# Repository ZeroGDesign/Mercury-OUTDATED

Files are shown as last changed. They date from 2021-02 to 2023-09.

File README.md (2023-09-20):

# UPDATE AUGUST 2022

The file configurators are live for our EVA 2.4 setup. Please use these from now on: [https://docs.zerog.one/manual/build/mercury_eva/printed_files#-mercury-one1-configurator](https://docs.zerog.one/manual/build/mercury_eva/printed_files#-mercury-one1-configurator)

Or find the cad files here: https://github.com/ZeroGDesign/docs/blob/gh-pages/docs/assets/stl/m1_1/mercury_235_assembly.step

# UPDATE

We're moving towards Mercury 1.1, this will support the Voron Stealthburner and Eva 2.4.

We'd like to recommend you to join our [Discord server](https://discord.io/zerog) for more info on how to build this. We're activly working on our documentation to make our project even better and easier to build for you. Please visit our [Documentation](https://docs.zerog.one/){:target="_blank"} to read more about our current projects.

## Documentation

The new files can be found on our [documentation](https://docs.zerog.one/) under section "manual"  We're activly working on the documentation to make your world easier.



ZeroGDesign/Mercury is licensed under the
GNU General Public License v3.0<br><br>
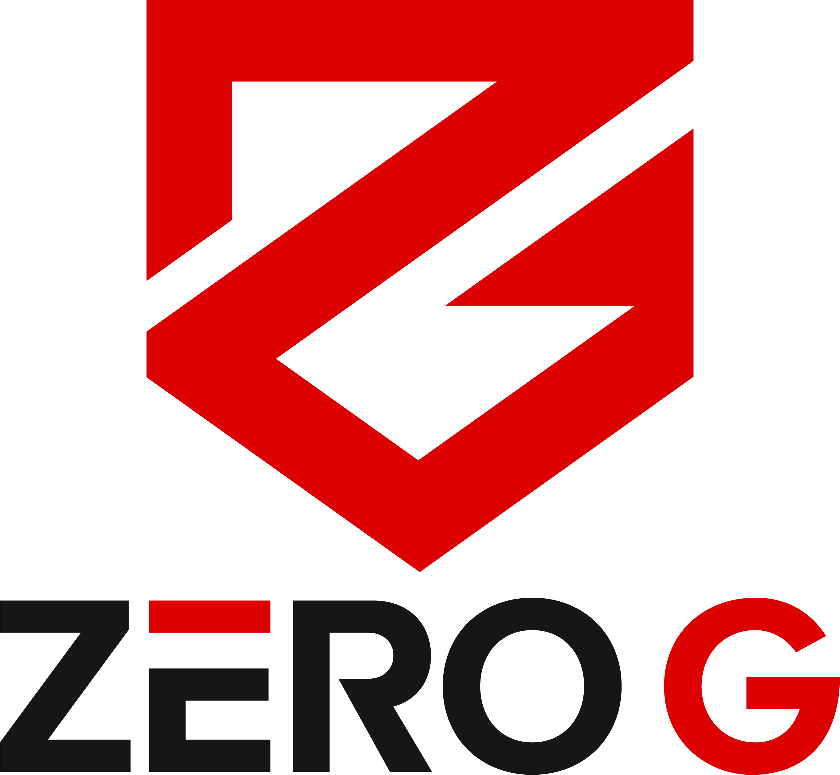
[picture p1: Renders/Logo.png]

____

### Mercury One
<a href="https://discord.io/zerog" target="_blank">Discord Shield</a>
<br>Website: https://zerogdesign.github.io/index.html
____
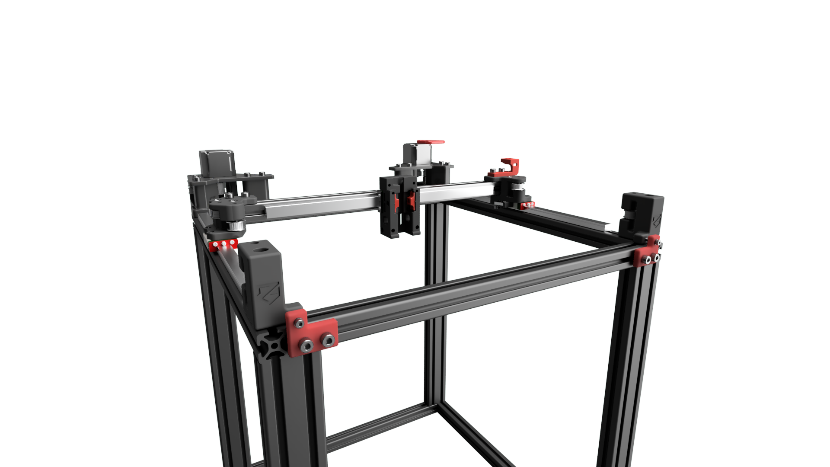
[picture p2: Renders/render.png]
<br><br>
The official release Zero G Mercury One 3D printer inspired by Voron.<br>
This project uses a 370mm x Extrusion and 3 x 300mm MGN12H rails<BR><BR>
Recommended print settings: https://i.imgur.com/dN6sj4v.png

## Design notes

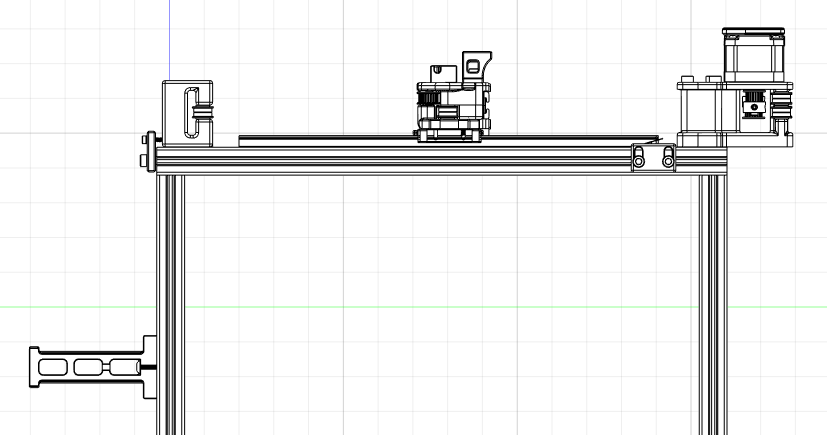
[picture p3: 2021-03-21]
Renders/right_side_view.png

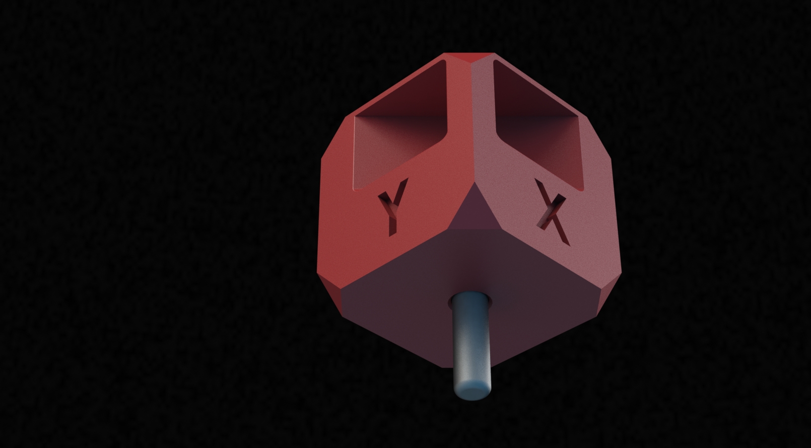
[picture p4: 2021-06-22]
Renders/Cube/ZeroGCube2.JPG

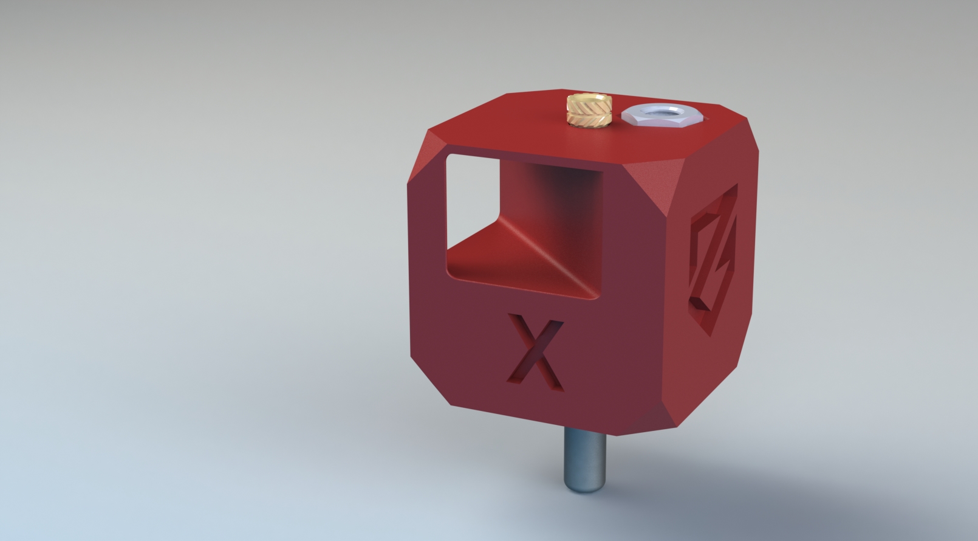
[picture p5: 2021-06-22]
Renders/Cube/ZeroGCube3.JPG

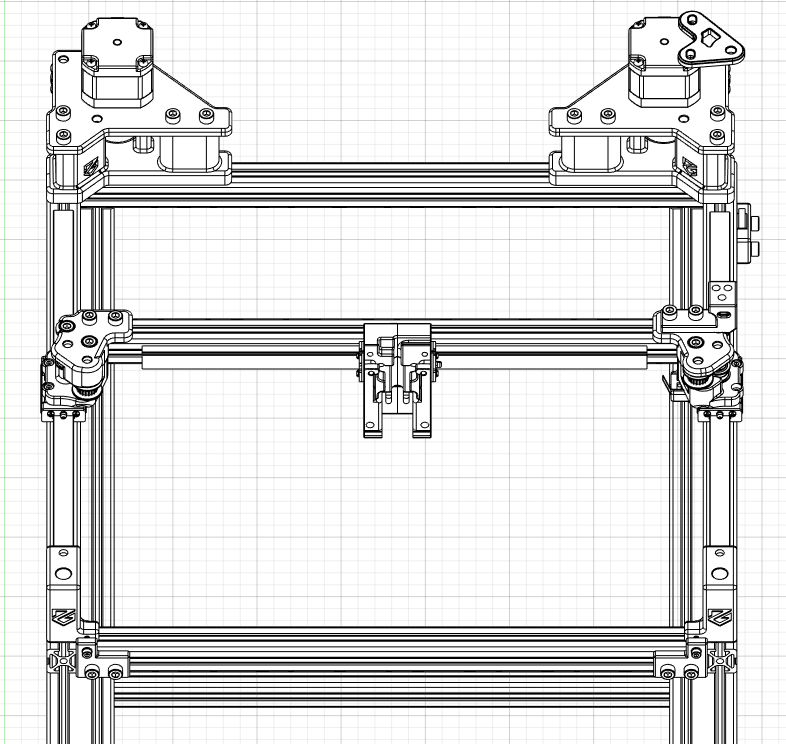
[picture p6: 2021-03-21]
Renders/front_top_view.png

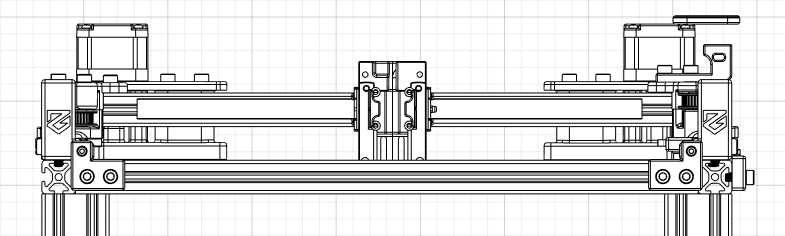
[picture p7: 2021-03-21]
Renders/front_view.png

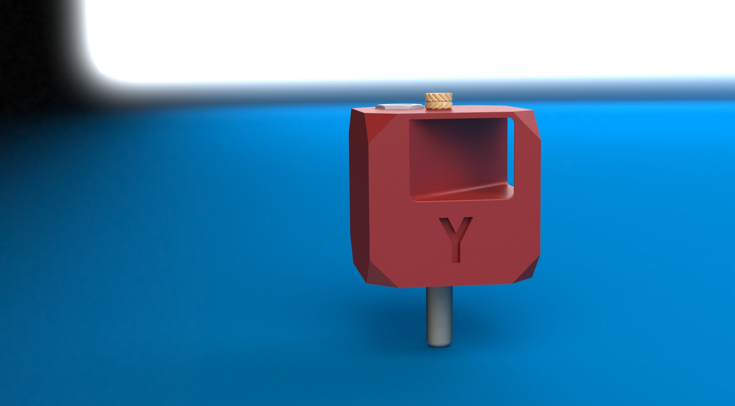
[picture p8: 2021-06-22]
Renders/Cube/ZeroGCube4.JPG

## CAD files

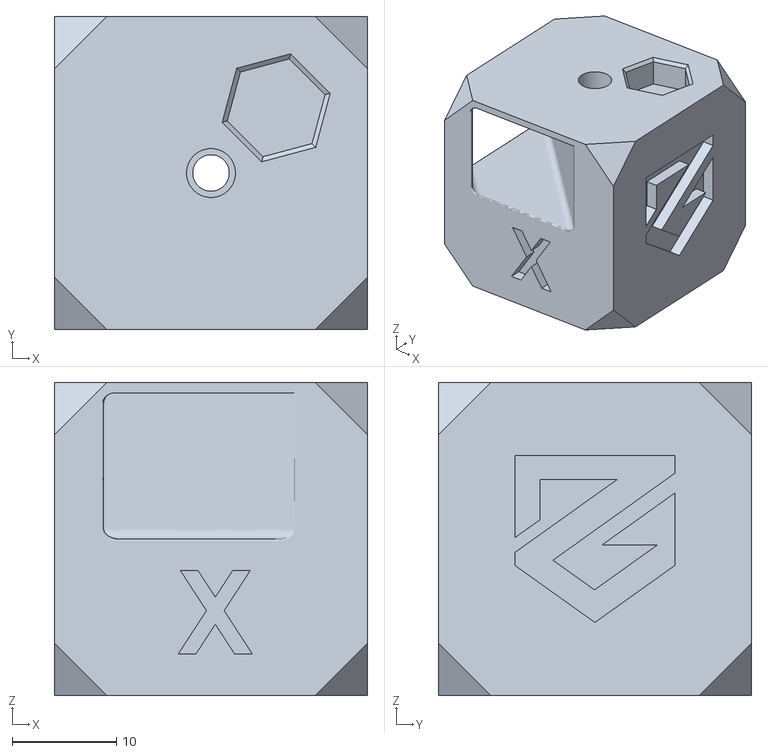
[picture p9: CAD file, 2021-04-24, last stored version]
STLs/CALIBRATION/ZeroGCube30x30.stl
30.0 x 30.0 x 30.0

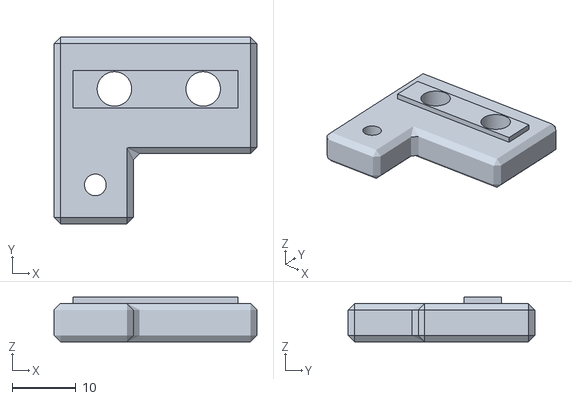
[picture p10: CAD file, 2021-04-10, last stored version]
STLs/MERCURY ONE/Front Idler Towers/Pulley_tension_left.stl
31.8 x 29.3 x 7.00

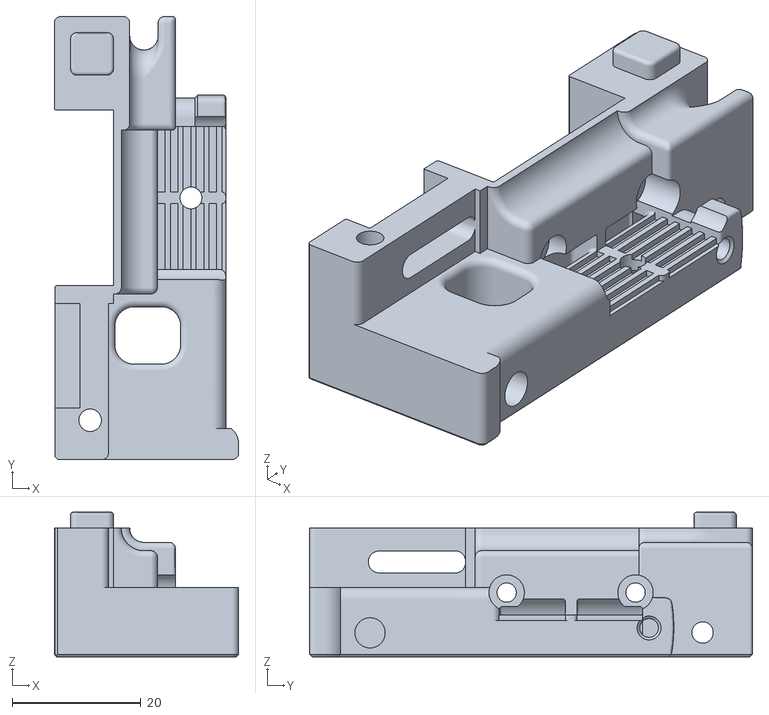
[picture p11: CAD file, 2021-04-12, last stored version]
STLs/MERCURY ONE/Gantry/AFTERBURNER MGN12H MOUNT (CUSTOM)/Right half.stl
28.6 x 68.8 x 22.5

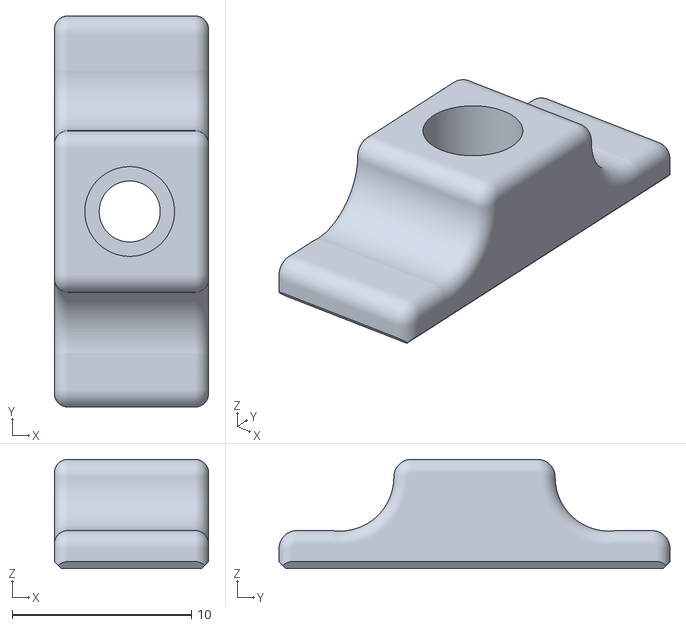
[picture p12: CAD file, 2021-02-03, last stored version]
STLs/MERCURY ONE/Gantry/X_Axis/X_Carriage/belt_clamp_x2.stl
8.60 x 21.8 x 6.10

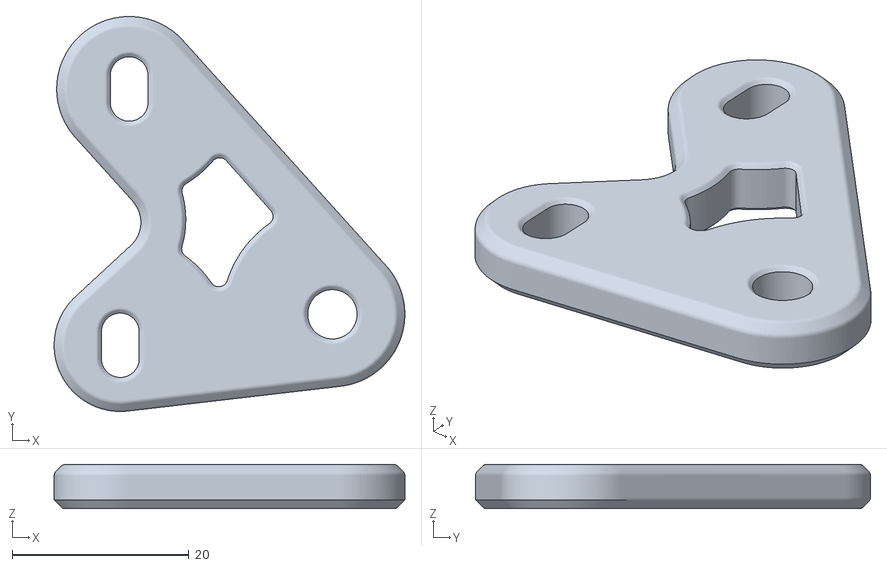
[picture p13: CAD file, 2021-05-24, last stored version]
STLs/MERCURY ONE/Stepper mounts/right_stepper_chain_mount_generic_optional.stl
39.7 x 44.7 x 5.00

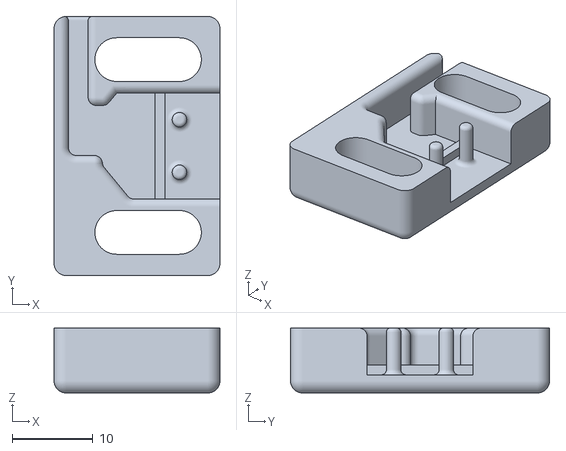
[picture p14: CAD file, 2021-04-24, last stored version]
STLs/MERCURY ONE/Y_Endstop.stl
20.5 x 32.0 x 8.02

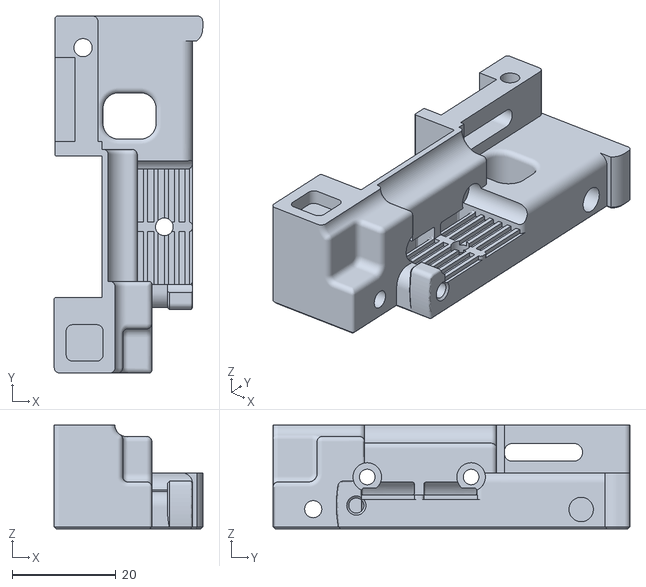
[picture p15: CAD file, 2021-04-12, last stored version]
STLs/MERCURY ONE/Gantry/AFTERBURNER MGN12H MOUNT (CUSTOM)/Left half.stl
28.6 x 68.8 x 20.0

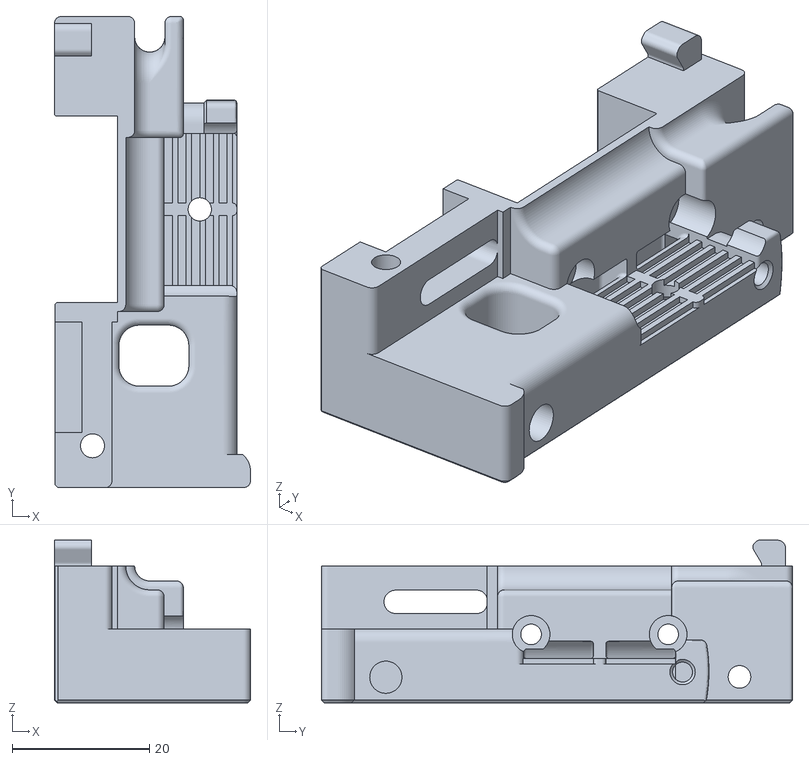
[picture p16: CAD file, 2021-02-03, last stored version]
STLs/MERCURY ONE/Gantry/X_Axis/X_Carriage/x_carriage_frame_right.stl
28.6 x 68.8 x 23.8

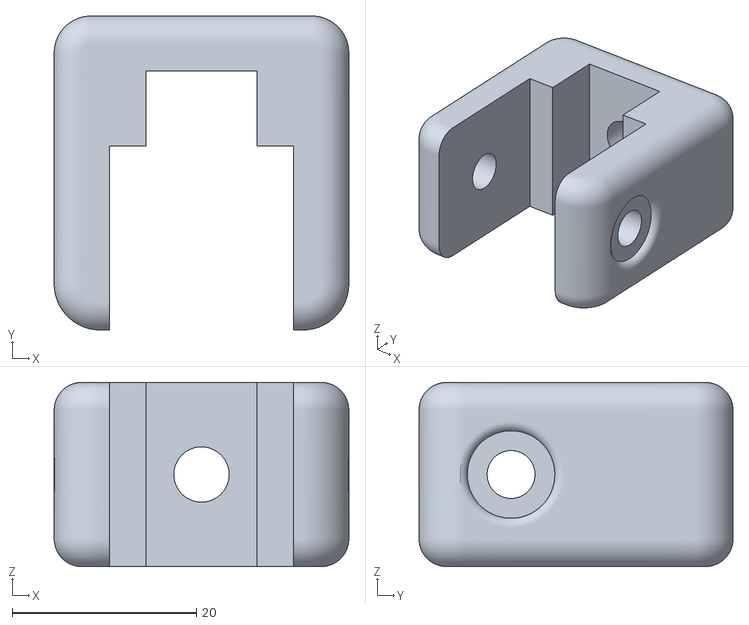
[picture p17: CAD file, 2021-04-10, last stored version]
STLs/MERCURY ONE/Rail alignment tool x 2.stl
32.0 x 34.1 x 20.0

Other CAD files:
STLs/MERCURY ONE/Front Idler Towers/Pulley_tension_right.stl
STLs/MERCURY ONE/Gantry/AFTERBURNER MGN12H MOUNT (CUSTOM)/CLIPX2.stl
STLs/MERCURY ONE/Gantry/X_Axis/X_Carriage/x_carriage_frame_left.stl
STLs/MERCURY1/Gantry/X_Axis/X_Carriage/test.stl
STLs/MERCURY1/Gantry/X_Axis/X_Carriage/x_carriage_frame_left.stl

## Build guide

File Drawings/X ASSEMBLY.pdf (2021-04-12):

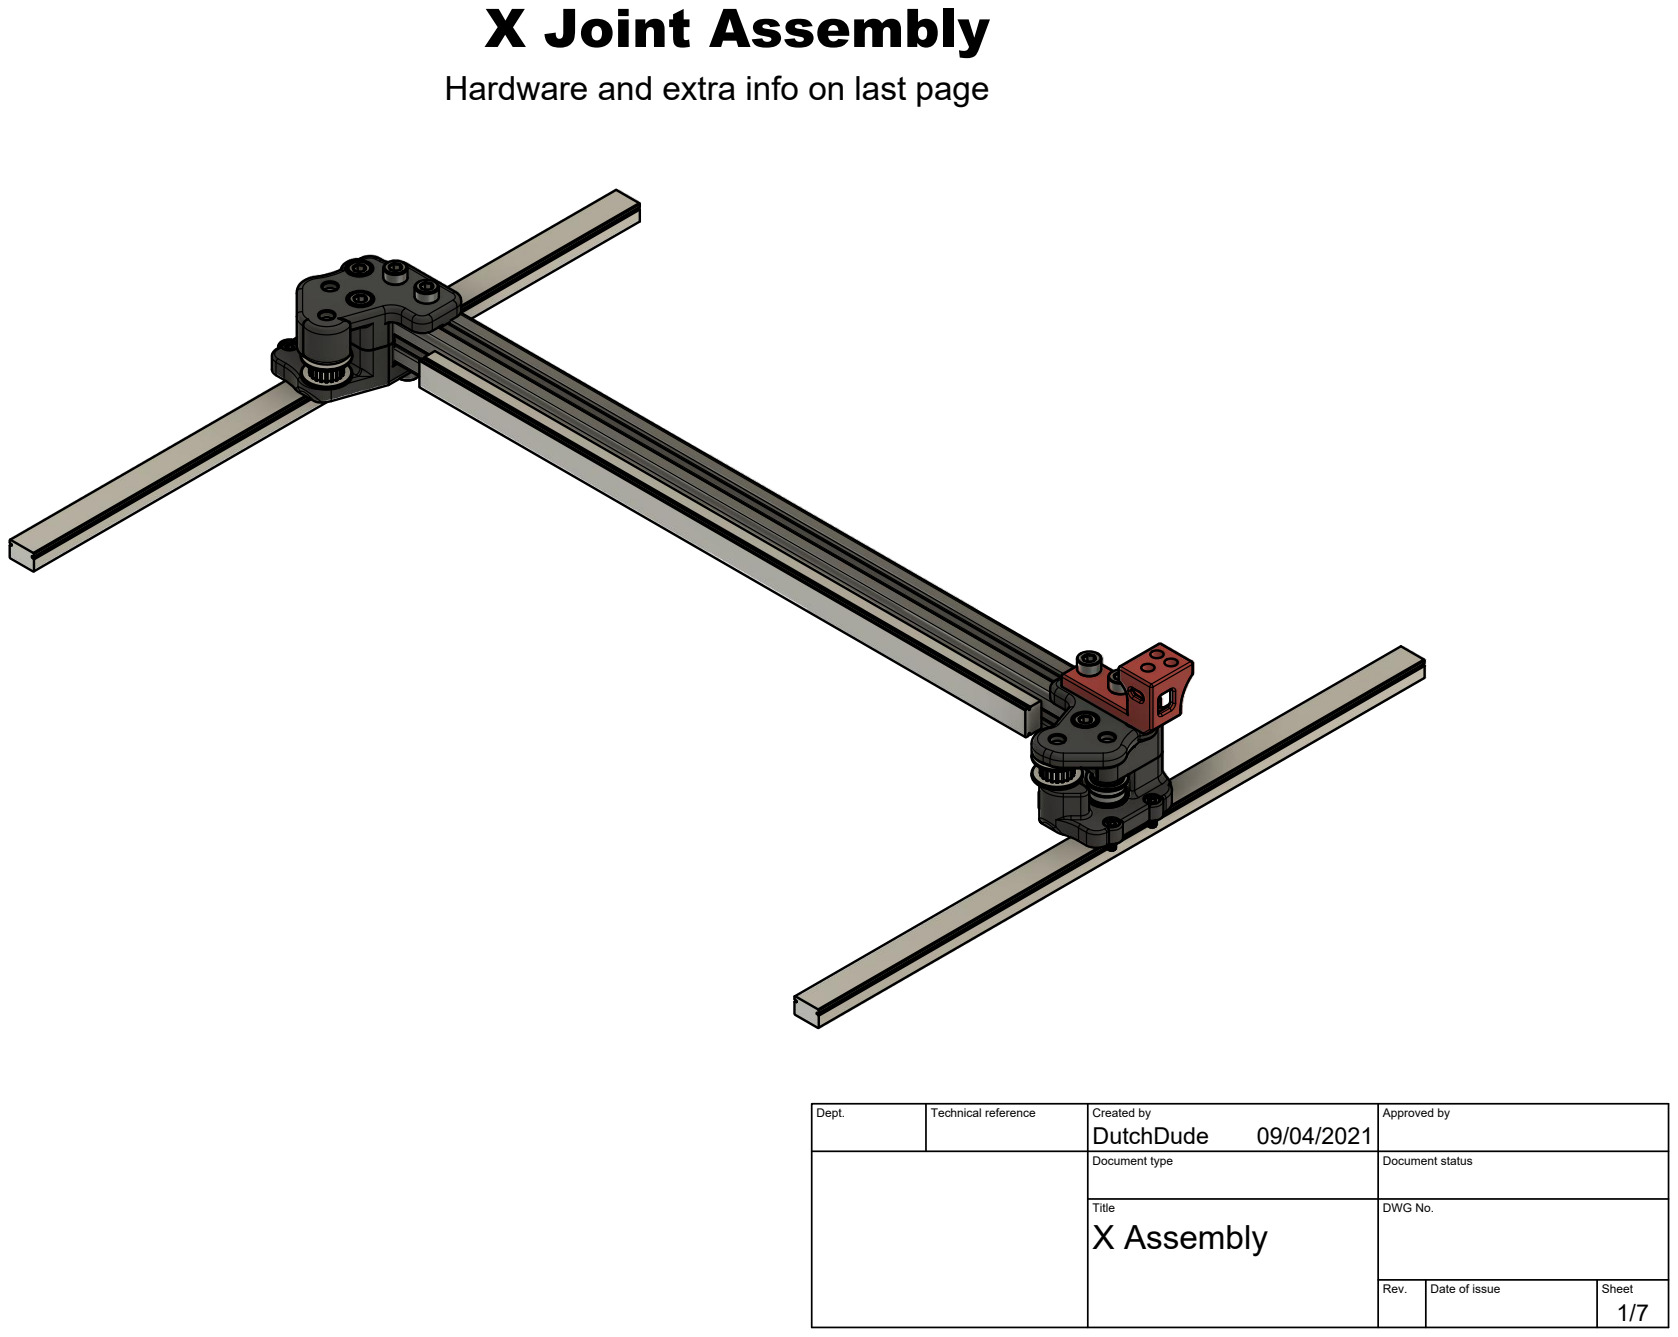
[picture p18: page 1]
X Joint Assembly

Hardware and extra info on last page

Dept. | Technical reference | Created by DutchDude 09/04/2021 | Approved by

Document type | Document status

Title X Assembly | DWG No.

Rev. | Date of issue | Sheet

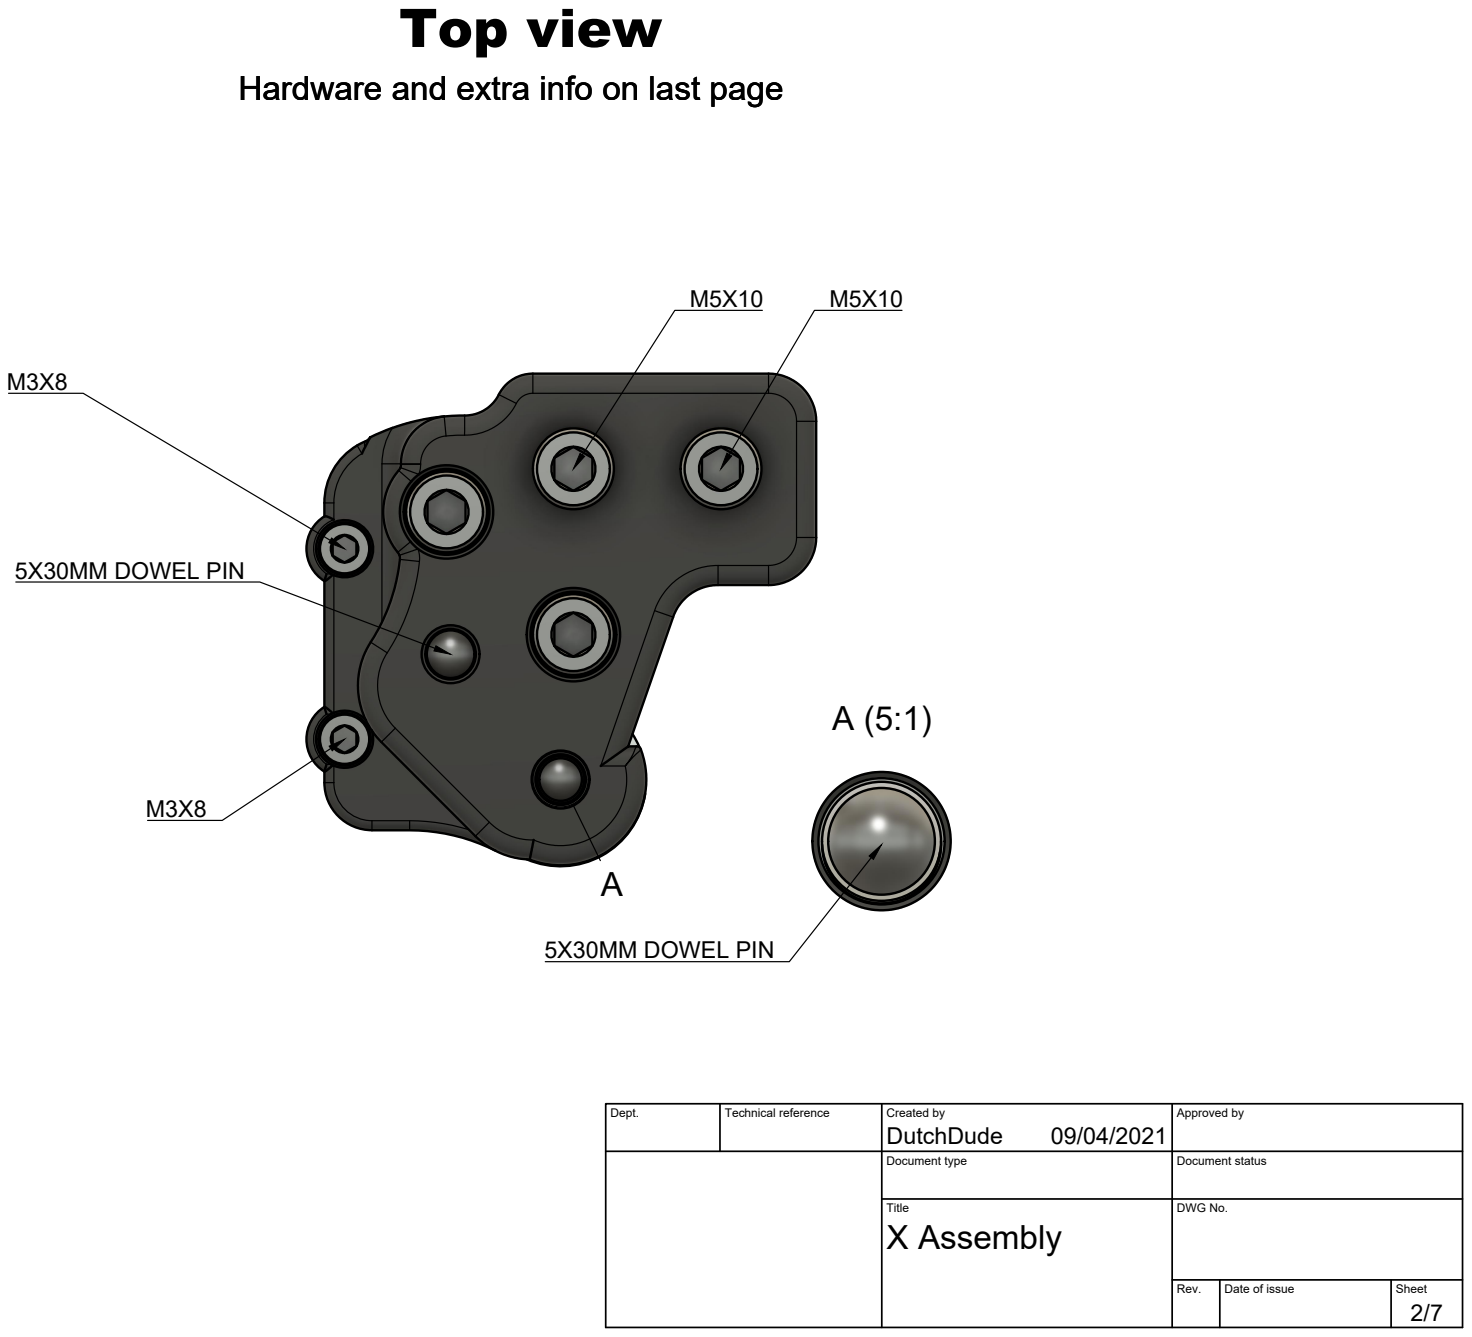
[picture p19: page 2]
Top view; 5X30MM DOWEL PIN

Hardware and extra info on last page

Dept. | Technical reference | Created by DutchDude 09/04/2021 | Approved by

Document type | Document status

Title X Assembly | DWG No.

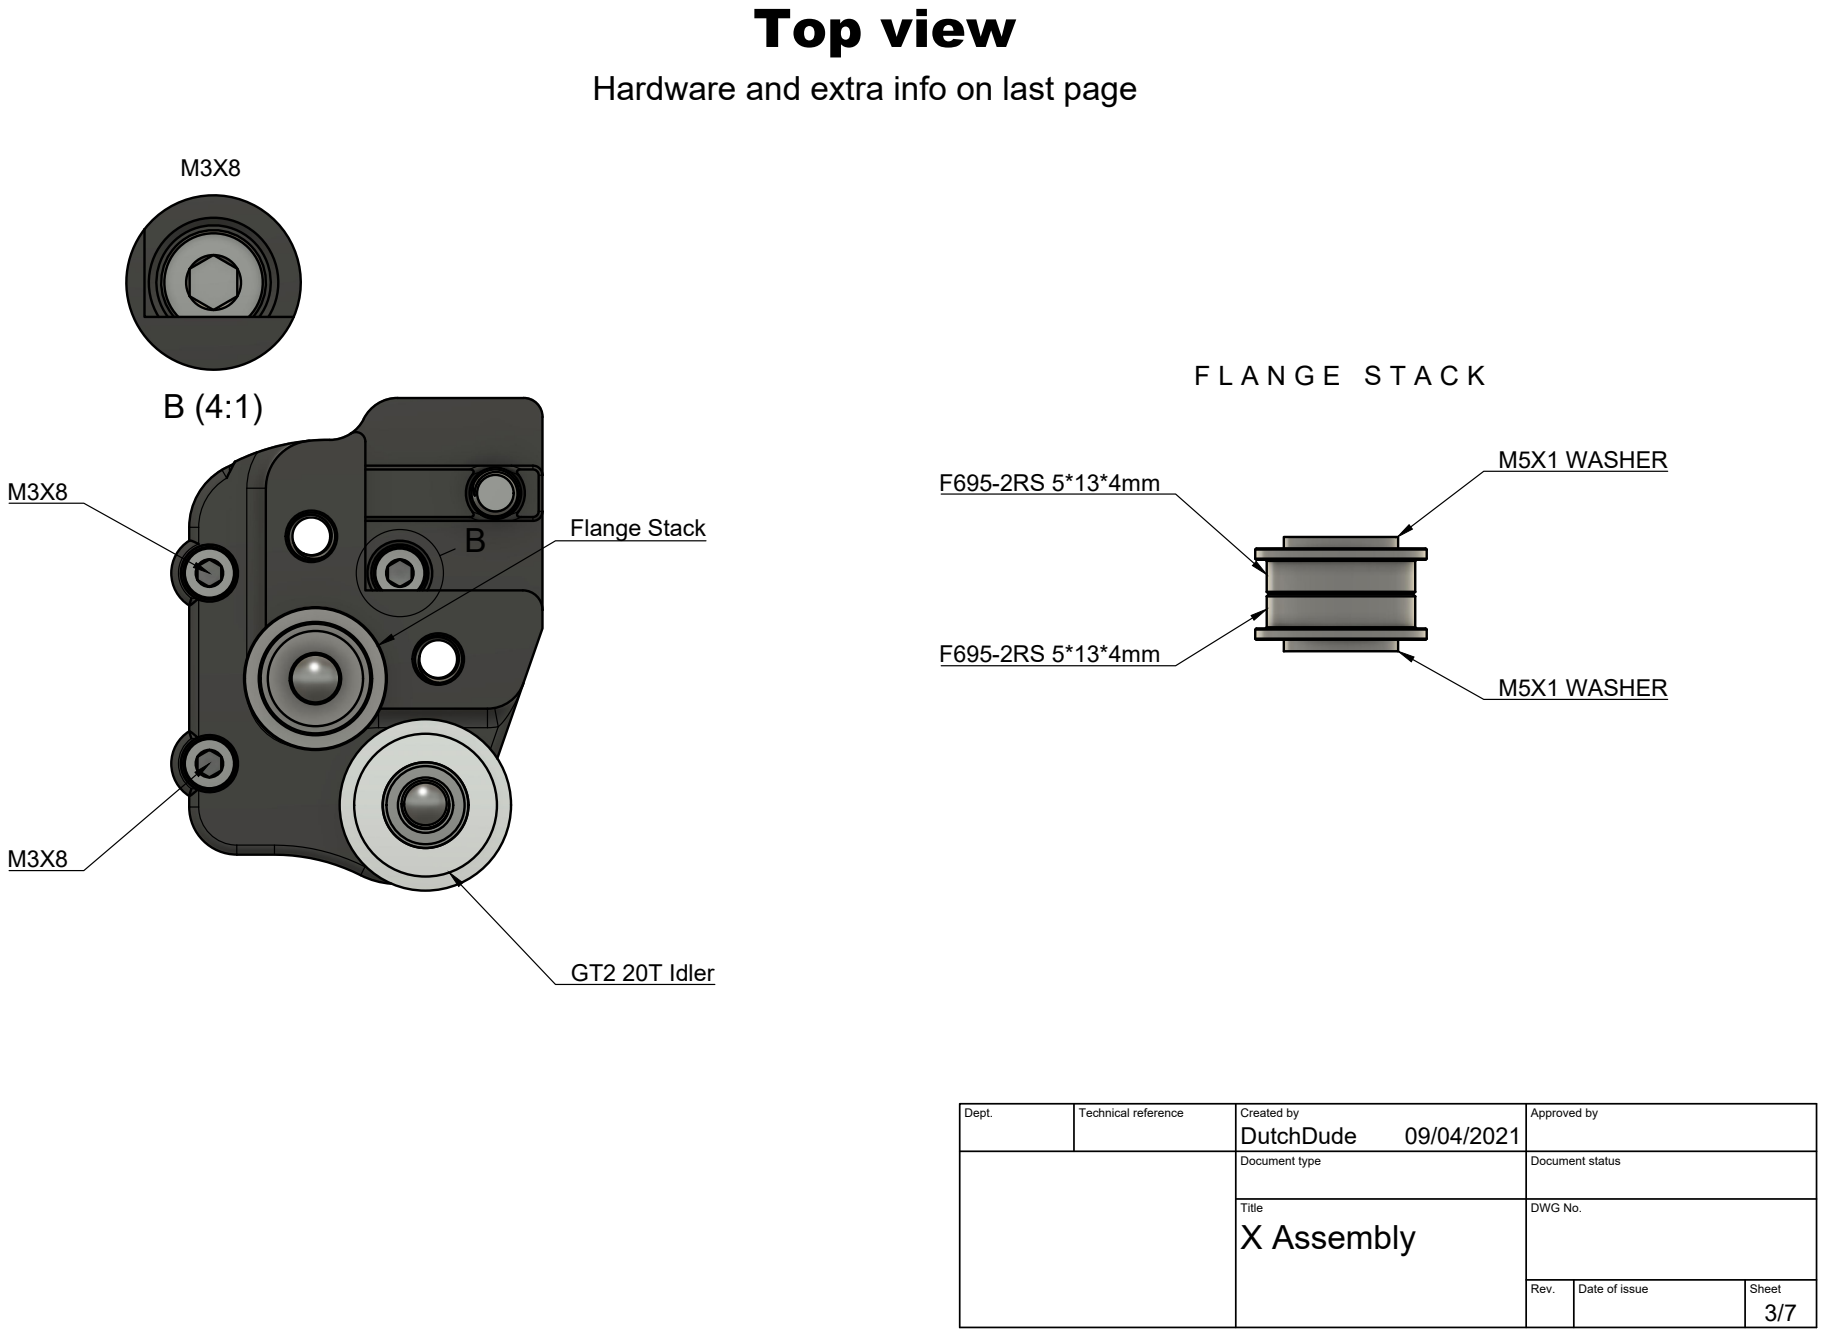
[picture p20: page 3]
Top view; Flange Stack; GT2 20T Idler; M5X1 WASHER

Hardware and extra info on last page

Dept. | Technical reference | Created by DutchDude 09/04/2021 | Approved by

Document type | Document status

Title X Assembly | DWG No.

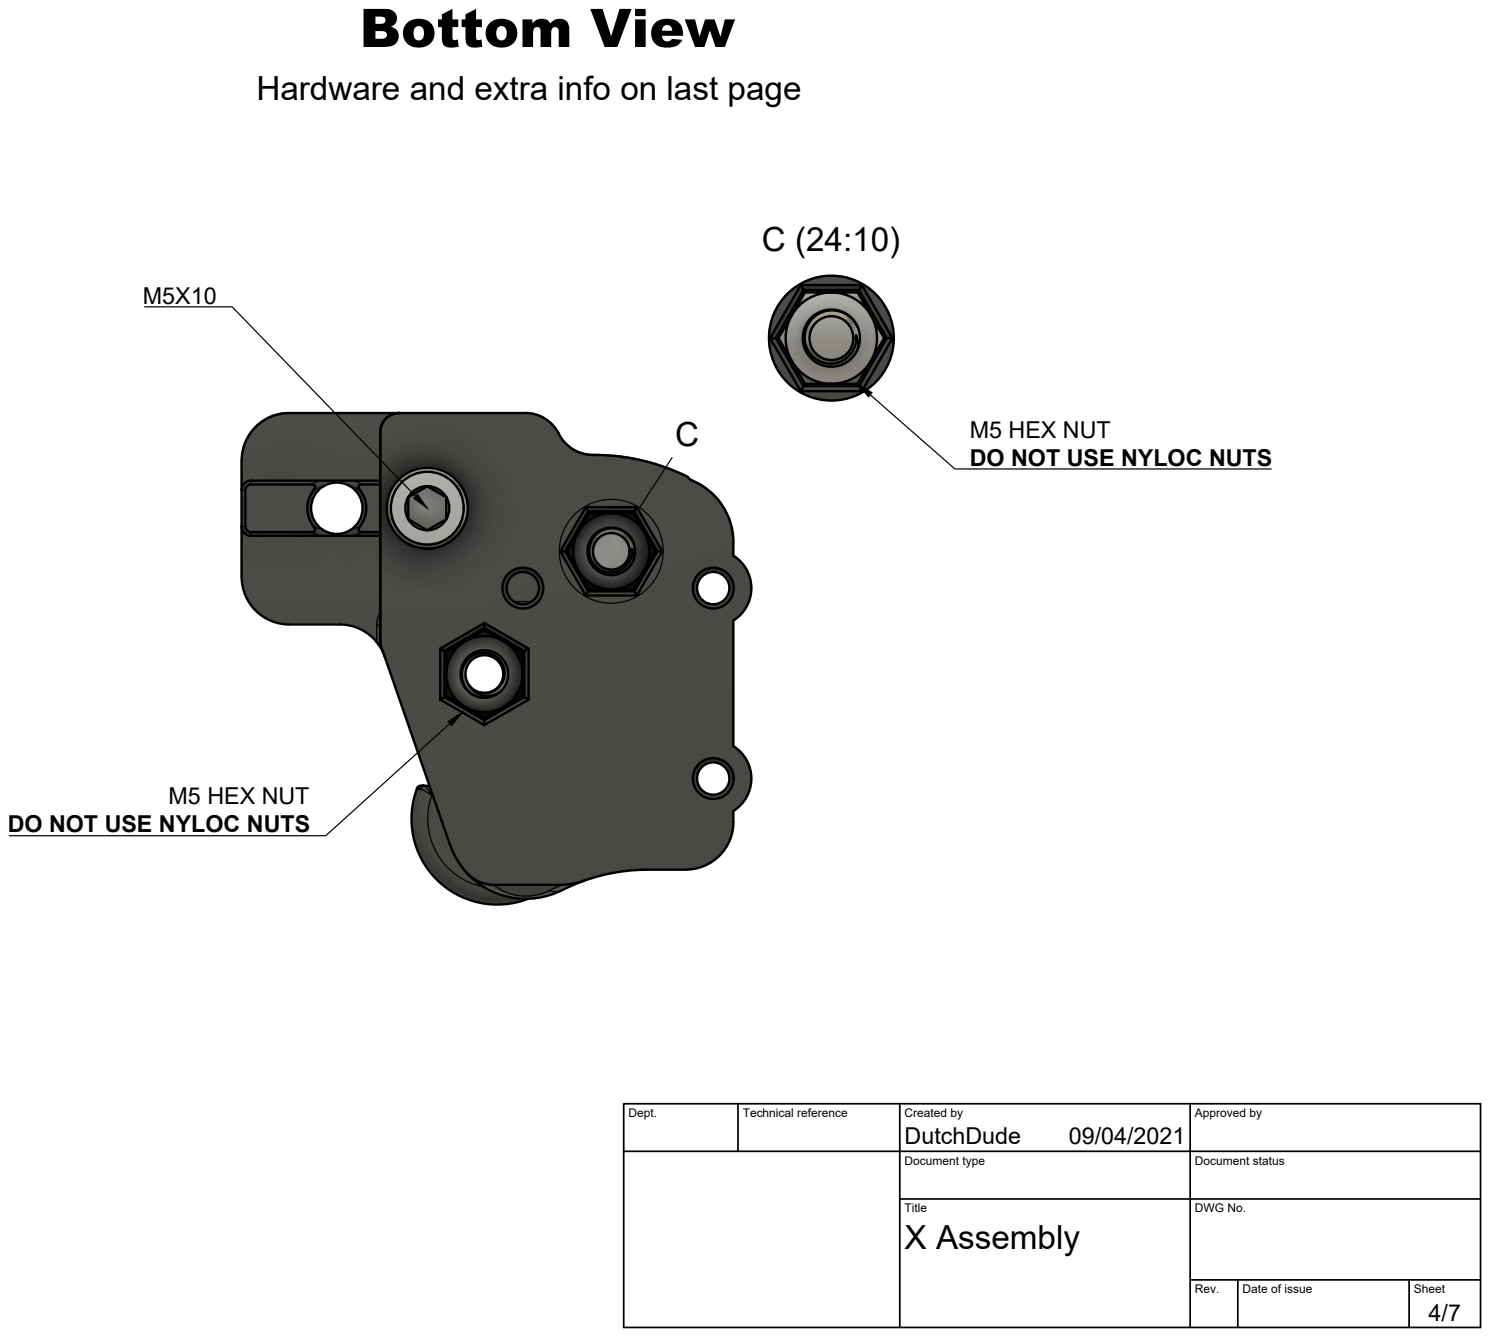
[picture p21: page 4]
Bottom View; M5 HEX NUT

Hardware and extra info on last page

M5 HEX NUT
DO NOT USE NYLOC NUTS

Dept. | Technical reference | Created by DutchDude 09/04/2021 | Approved by

Document type | Document status

Title X Assembly | DWG No.

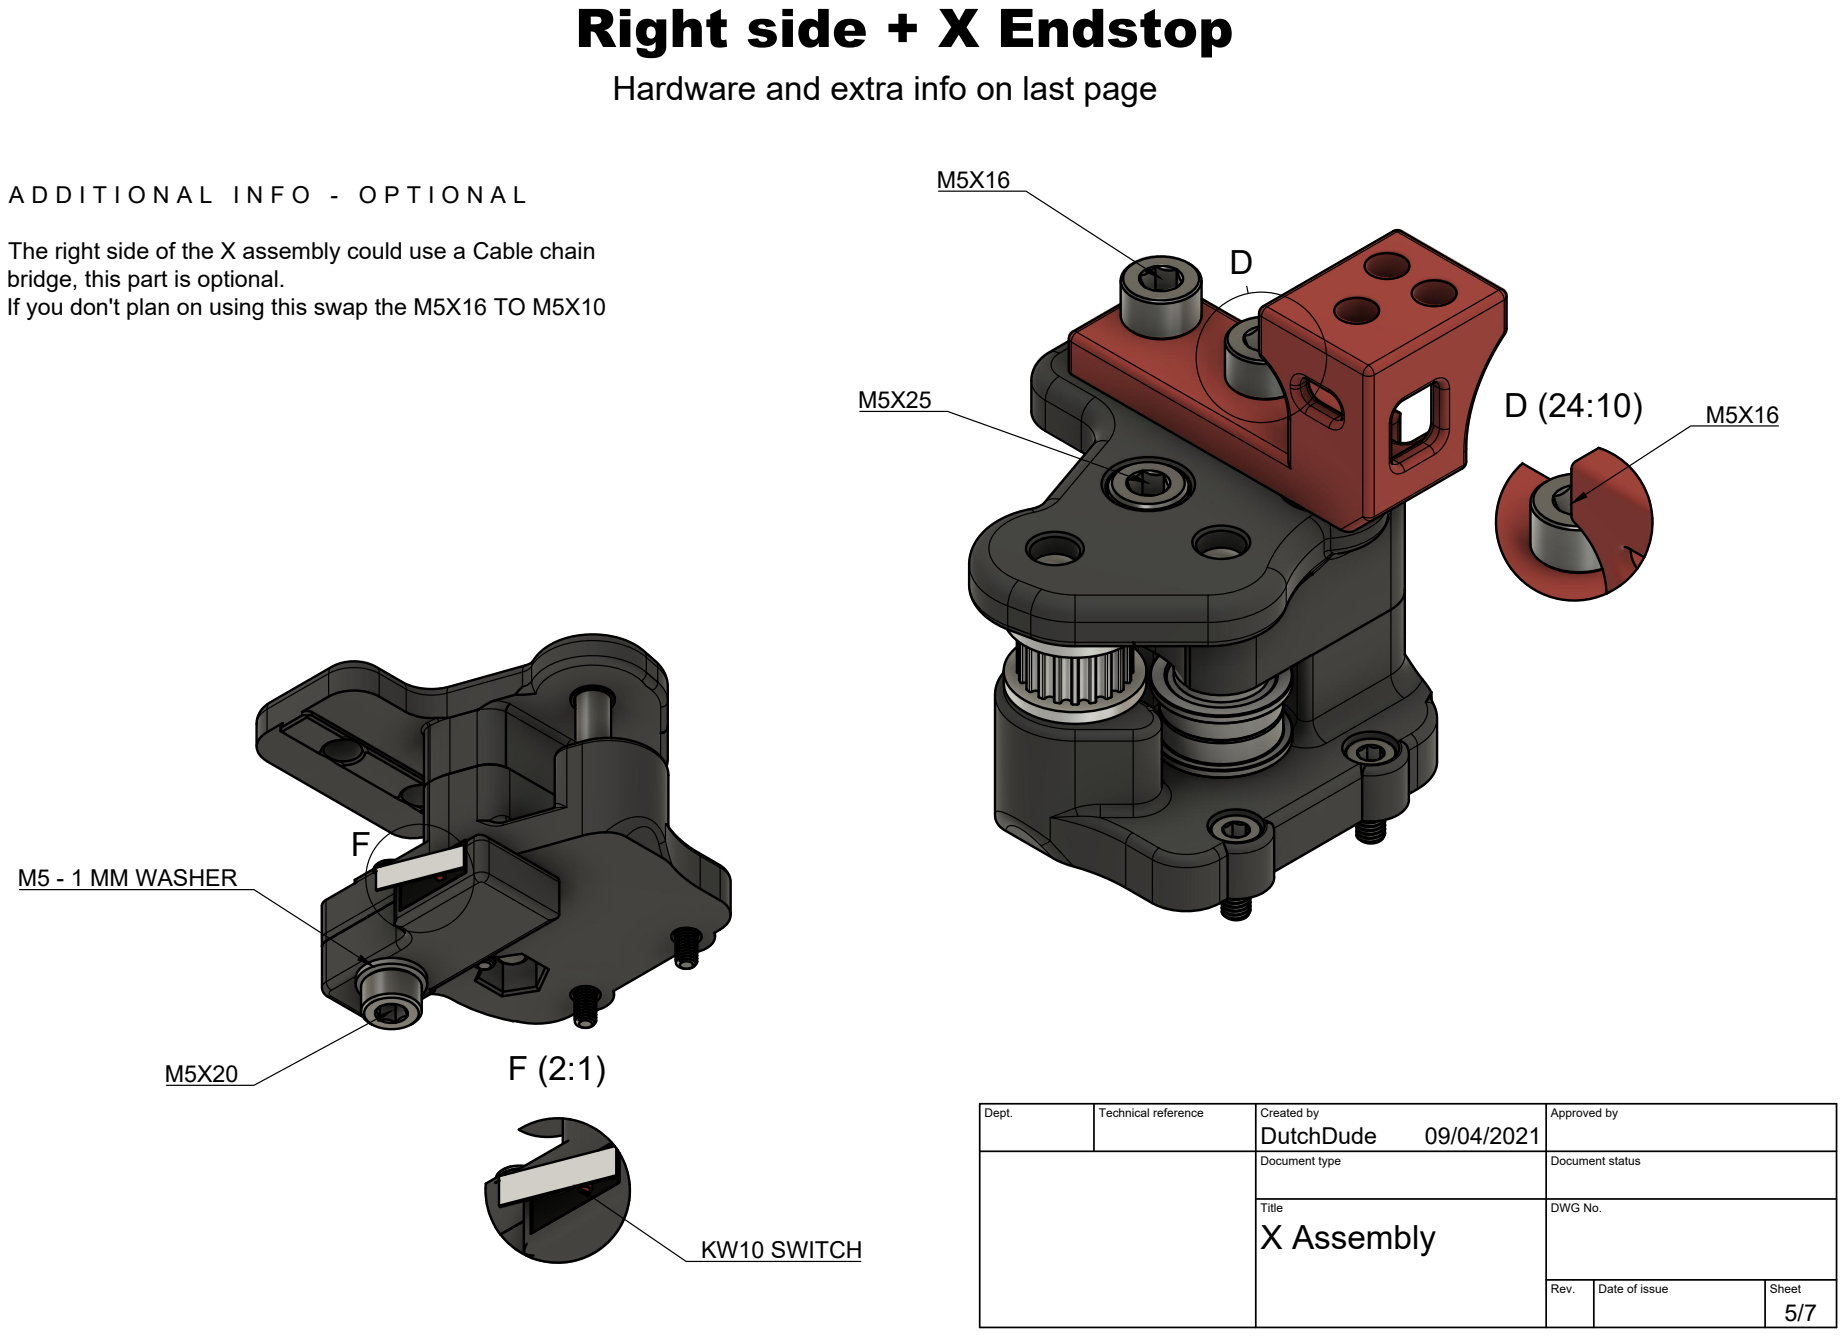
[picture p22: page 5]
KW10 SWITCH; M5 - 1 MM WASHER

Right side + X Endstop

Hardware and extra info on last page

The right side of the X assembly could use a Cable chain
bridge, this part is optional.
If you don't plan on using this swap the M5X16 TO M5X10

Dept. | Technical reference | Created by DutchDude 09/04/2021 | Approved by

Document type | Document status

Title X Assembly | DWG No.

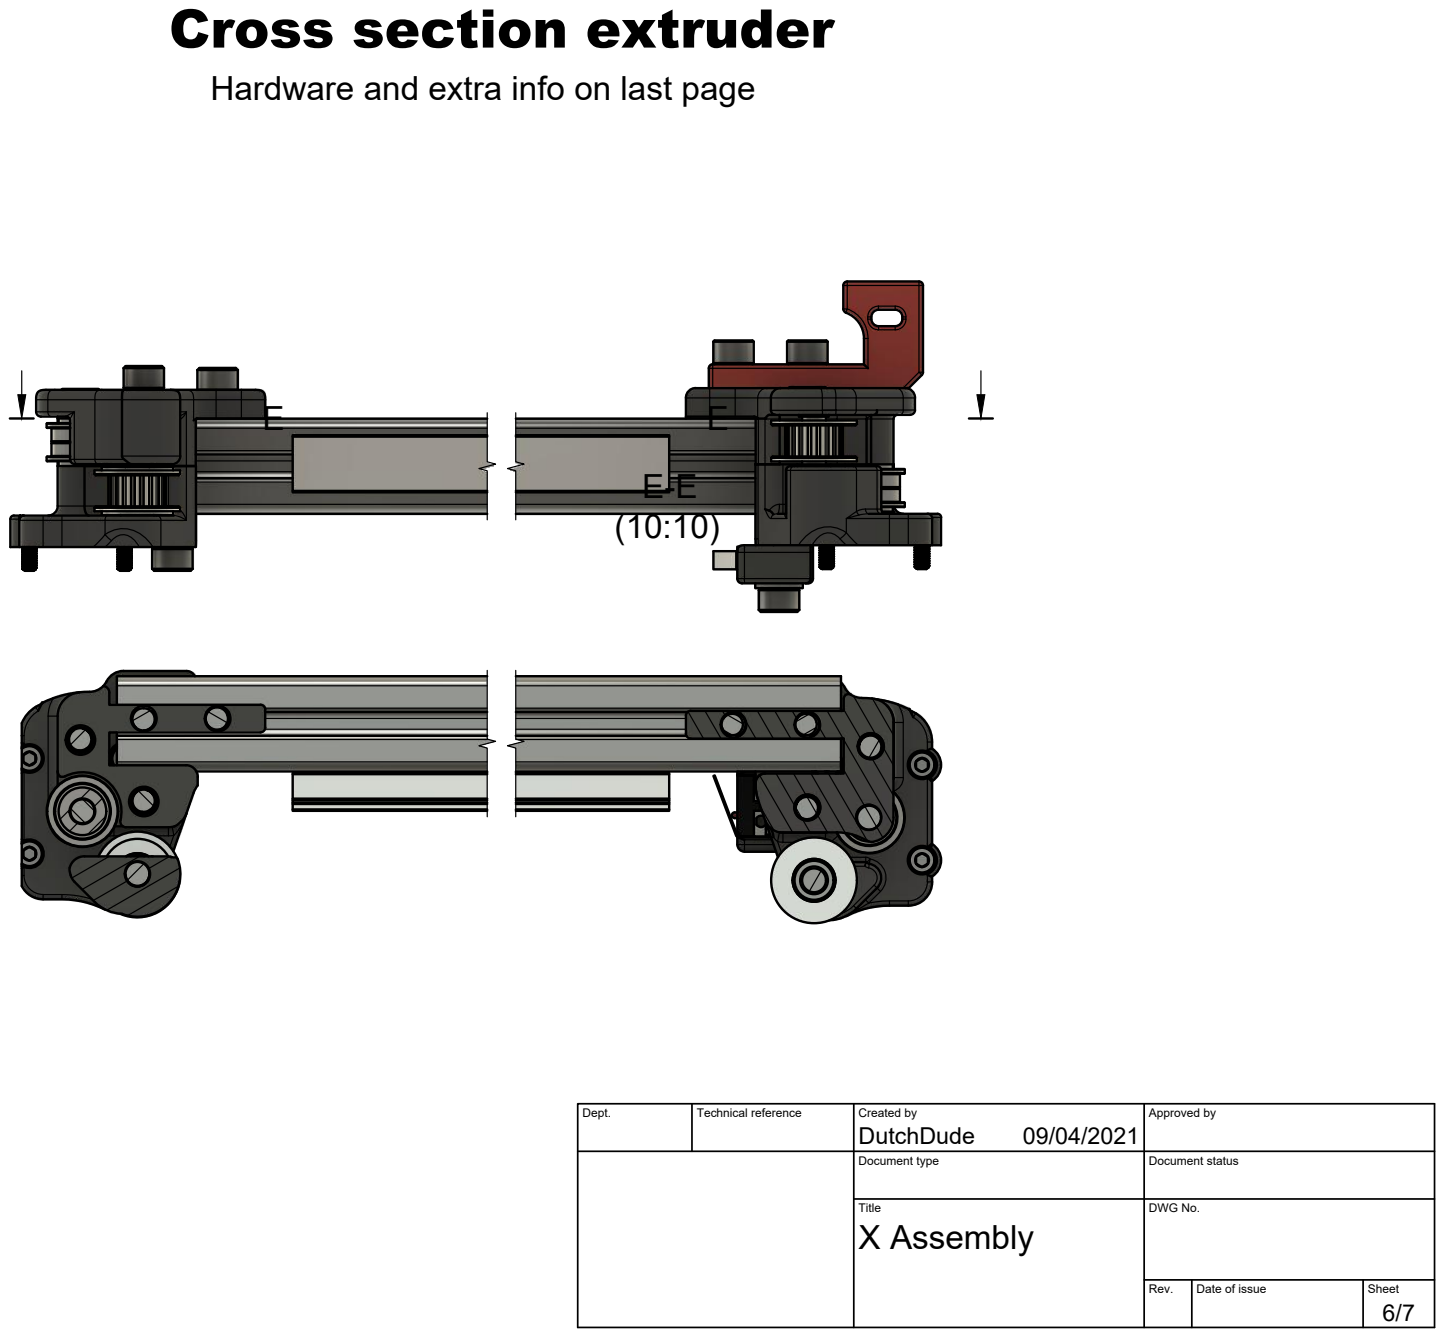
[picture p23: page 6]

Cross section extruder

Hardware and extra info on last page

Dept. | Technical reference | Created by DutchDude 09/04/2021 | Approved by

Document type | Document status

Title X Assembly | DWG No.

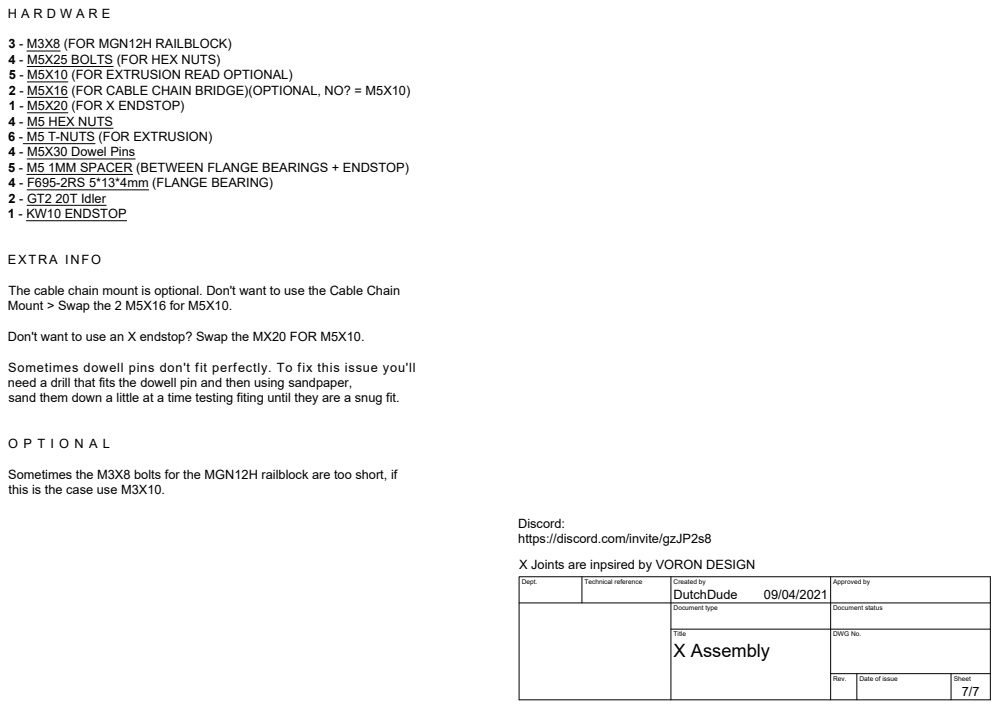
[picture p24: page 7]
EXTRA INFO

3 - M3X8 (FOR MGN12H RAILBLOCK)
4 - M5X25 BOLTS (FOR HEX NUTS)
5 - M5X10 (FOR EXTRUSION READ OPTIONAL)
2 - M5X16 (FOR CABLE CHAIN BRIDGE)(OPTIONAL, NO? = M5X10)
1 - M5X20 (FOR X ENDSTOP)
4 - M5 HEX NUTS
6 - M5 T-NUTS (FOR EXTRUSION)
4 - M5X30 Dowel Pins
5 - M5 1MM SPACER (BETWEEN FLANGE BEARINGS + ENDSTOP)
4 - F695-2RS 5*13*4mm (FLANGE BEARING)
2 - GT2 20T Idler
1 - KW10 ENDSTOP

The cable chain mount is optional. Don't want to use the Cable Chain
Mount > Swap the 2 M5X16 for M5X10.

Don't want to use an X endstop? Swap the MX20 FOR M5X10.

Sometimes dowell pins don't fit perfectly. To fix this issue you'll
need a drill that fits the dowell pin and then using sandpaper,
sand them down a little at a time testing fiting until they are a snug fit.

Sometimes the M3X8 bolts for the MGN12H railblock are too short, if
this is the case use M3X10.

Discord:
https://discord.com/invite/gzJP2s8

X Joints are inpsired by VORON DESIGN

Dept. | Technical reference | Created by DutchDude 09/04/2021 | Approved by

Document type | Document status

Title X Assembly | DWG No.

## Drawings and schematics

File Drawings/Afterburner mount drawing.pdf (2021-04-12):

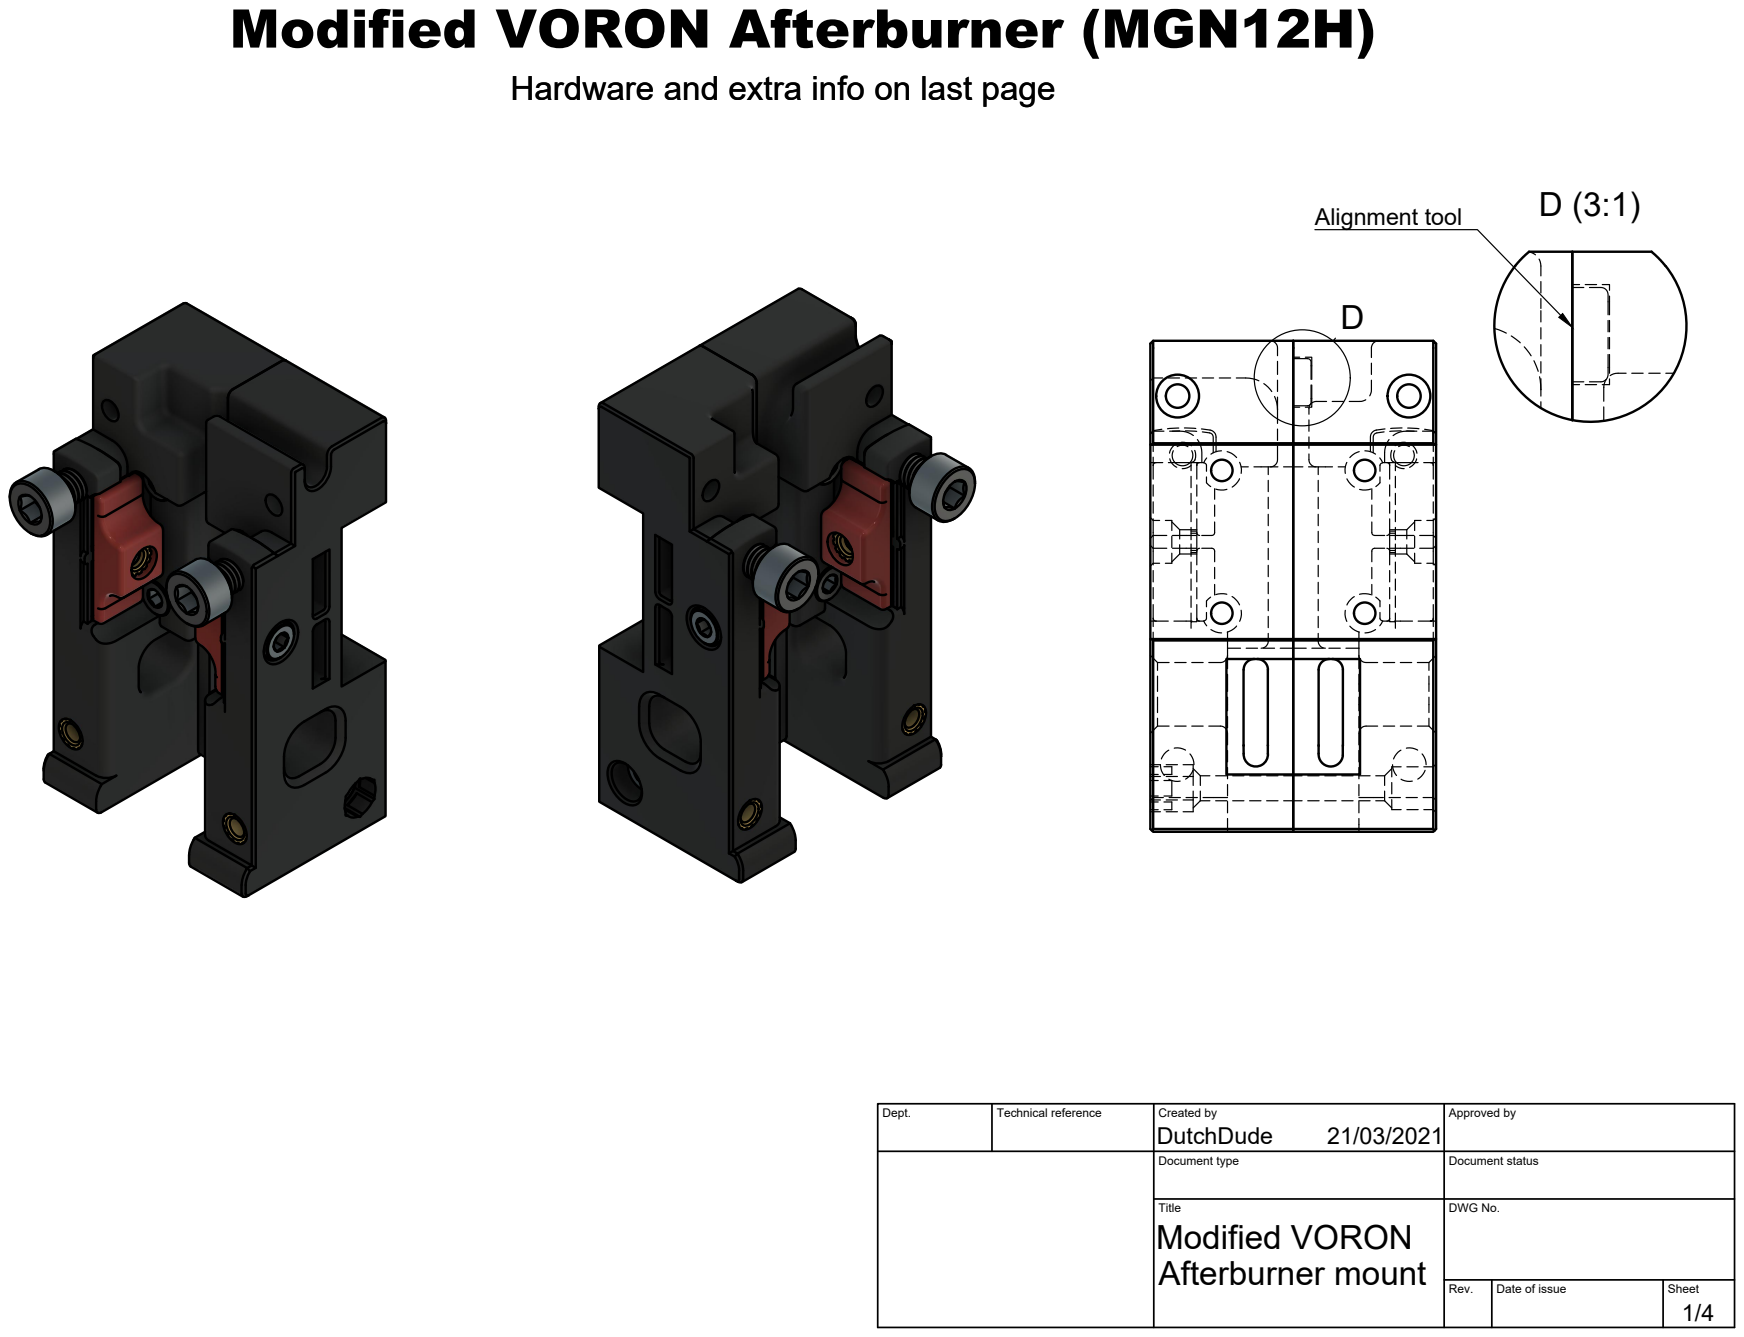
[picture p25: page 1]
D (3:1) Alignment tool

Modified VORON Afterburner (MGN12H)

Hardware and extra info on last page

Dept. | Technical reference | Created by DutchDude 21/03/2021 | Approved by

Document type | Document status

Title Modified VORON Afterburner mount | DWG No.

Rev. | Date of issue | Sheet

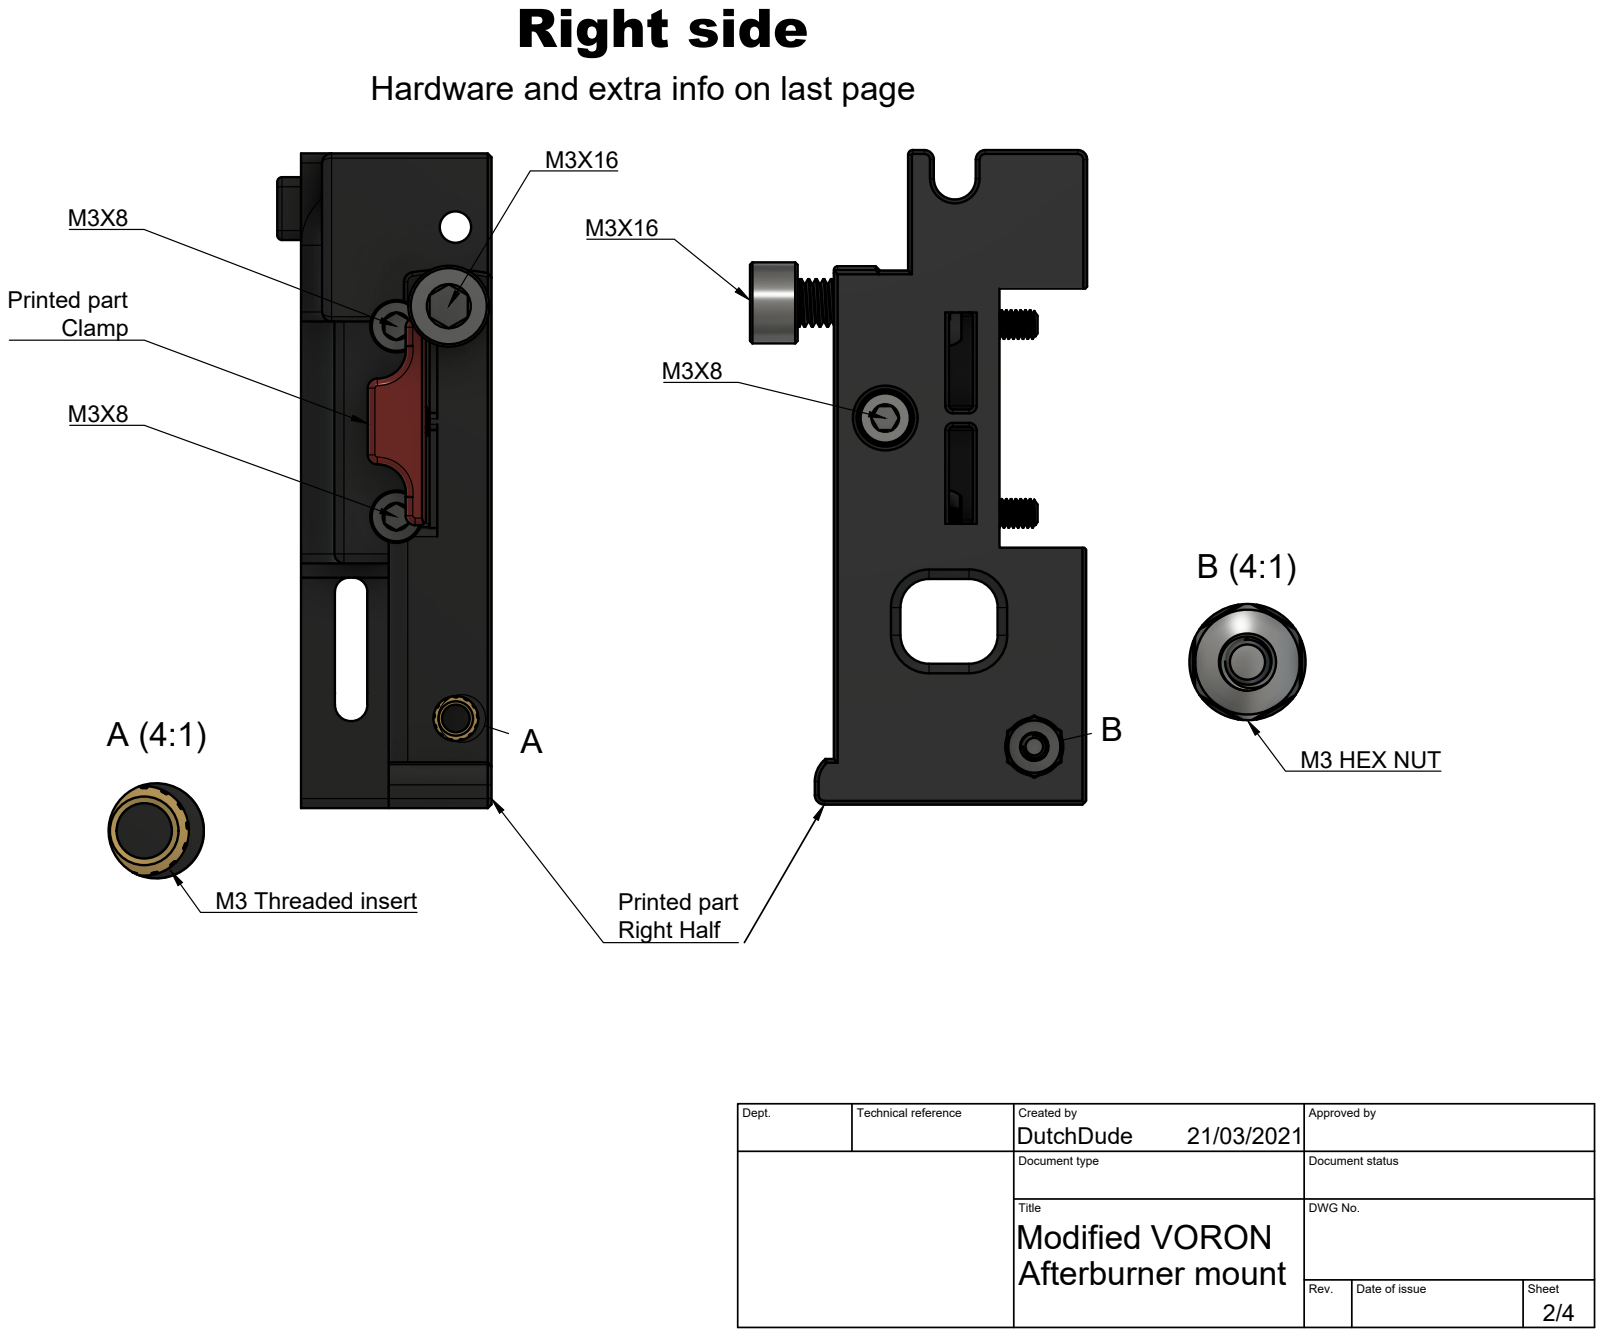
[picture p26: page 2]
Right side; Printed part Right Half; M3 HEX NUT; M3 Threaded insert; Printed part

Hardware and extra info on last page

Dept. | Technical reference | Created by DutchDude 21/03/2021 | Approved by

Document type | Document status

Title Modified VORON | DWG No.

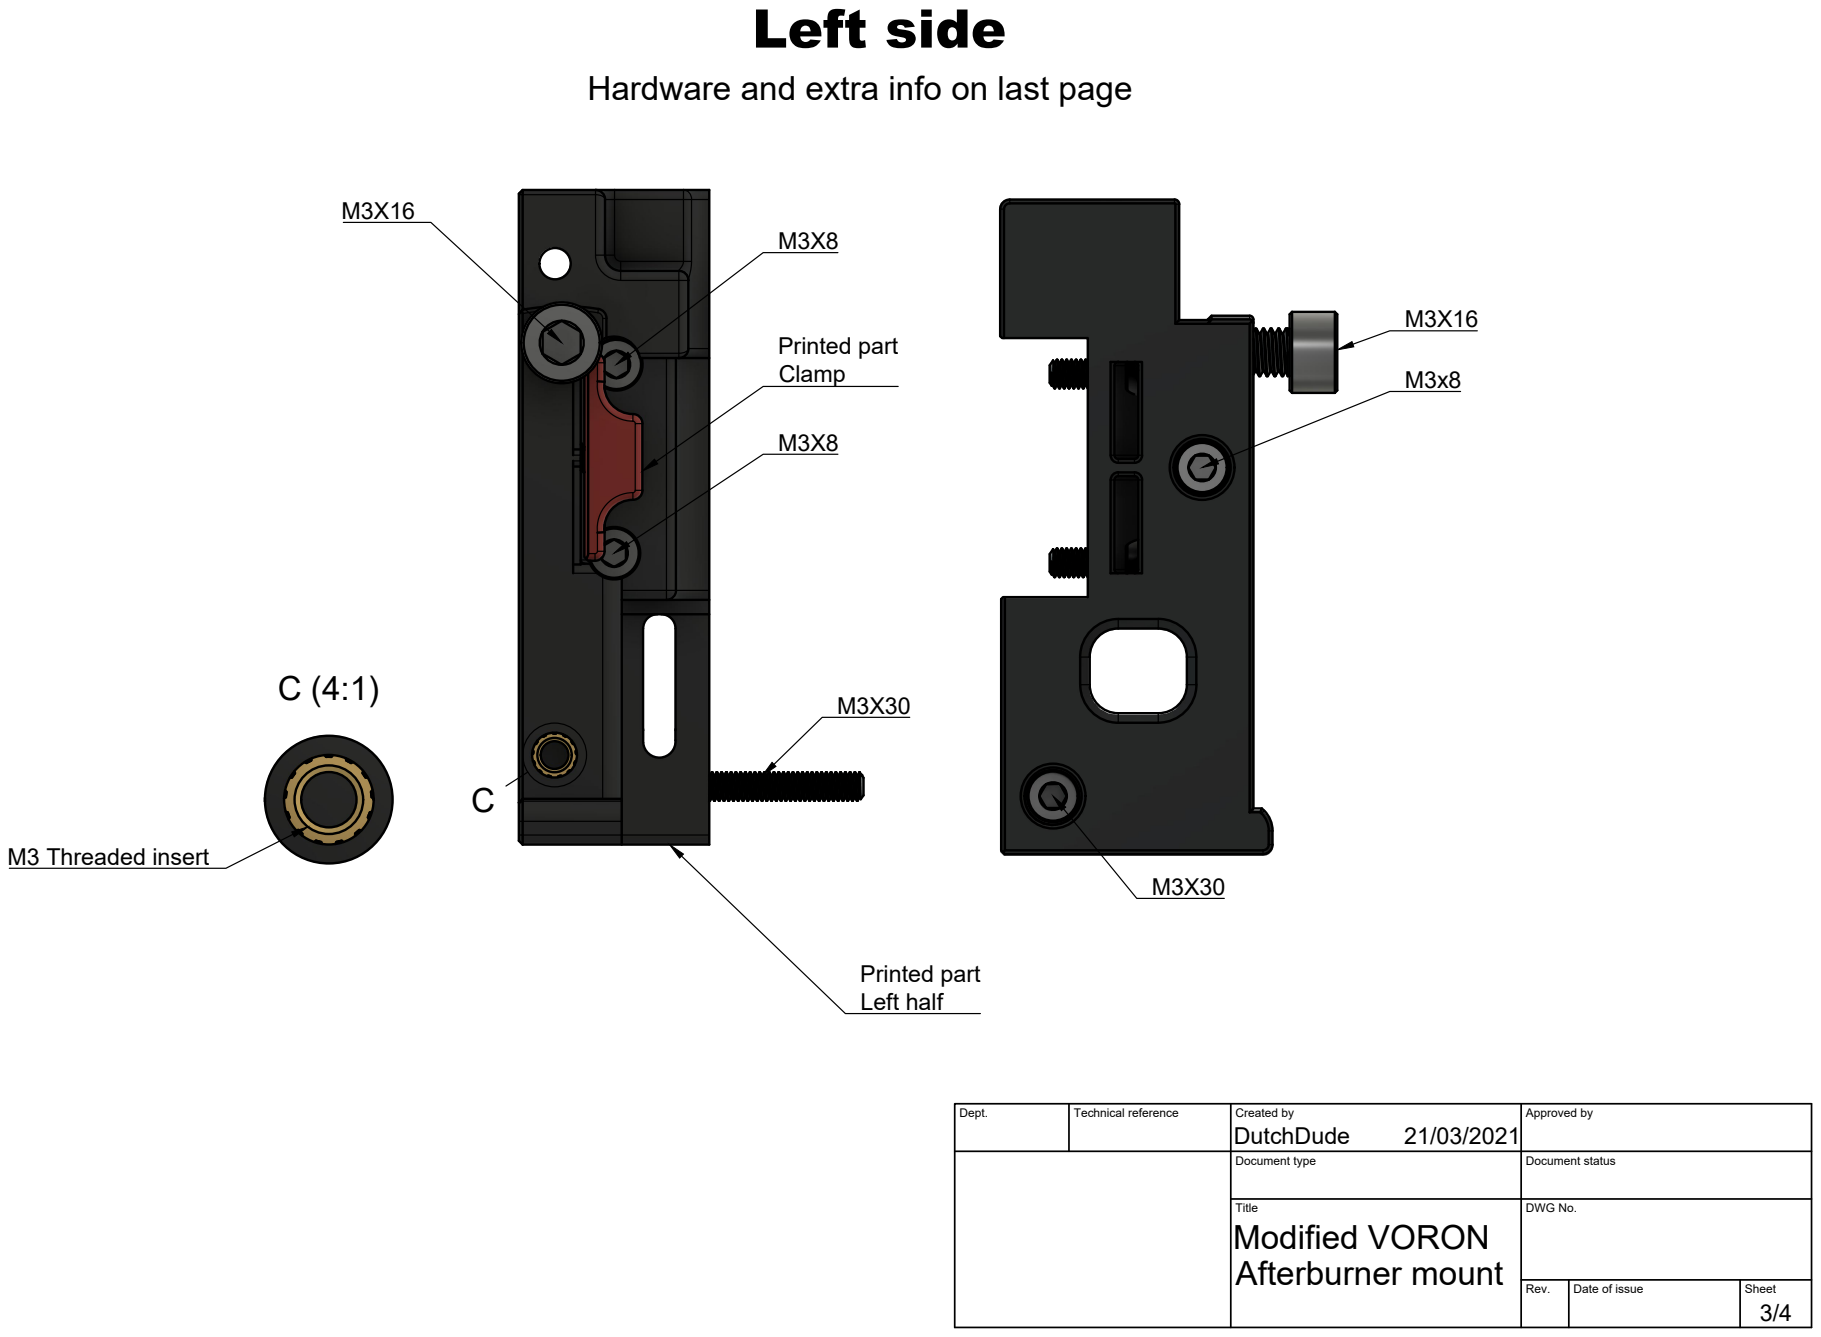
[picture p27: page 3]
Left side; Printed part Left half; Printed part; M3 Threaded insert

Hardware and extra info on last page

Dept. | Technical reference | Created by DutchDude 21/03/2021 | Approved by

Document type | Document status

Title Modified VORON | DWG No.

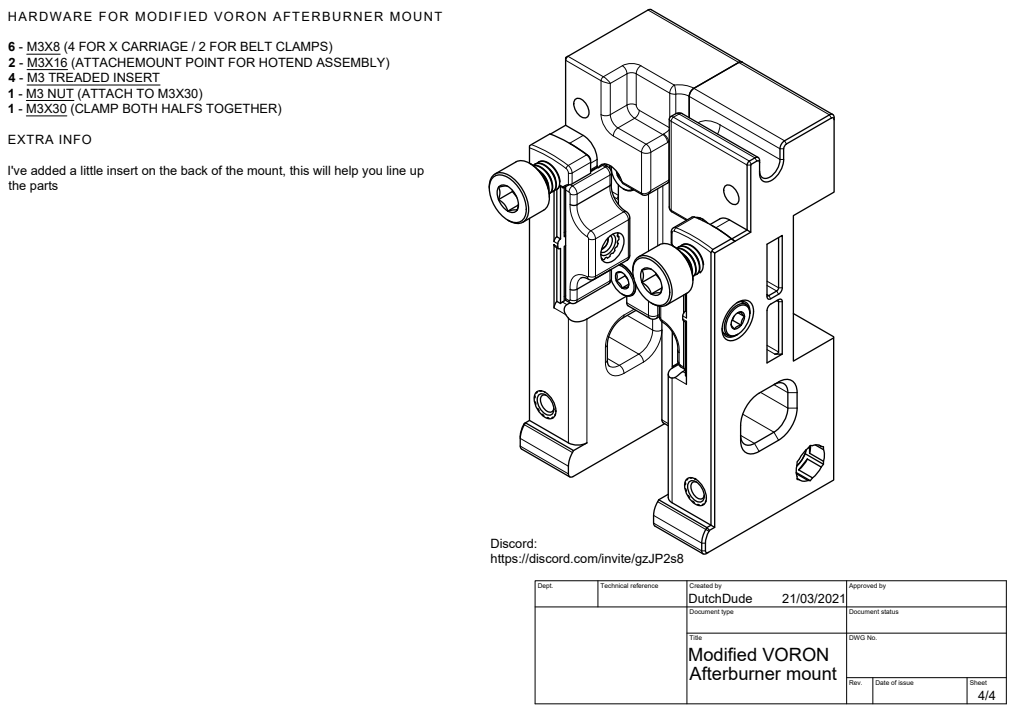
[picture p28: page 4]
EXTRA INFO

HARDWARE FOR MODIFIED VORON AFTERBURNER MOUNT

6 - M3X8 (4 FOR X CARRIAGE / 2 FOR BELT CLAMPS)
2 - M3X16 (ATTACHEMOUNT POINT FOR HOTEND ASSEMBLY)
4 - M3 TREADED INSERT
1 - M3 NUT (ATTACH TO M3X30)
1 - M3X30 (CLAMP BOTH HALFS TOGETHER)

I've added a little insert on the back of the mount, this will help you line up
the parts

Discord:
https://discord.com/invite/gzJP2s8

Dept. | Technical reference | Created by DutchDude 21/03/2021 | Approved by

Document type | Document status

Title Modified VORON | DWG No.

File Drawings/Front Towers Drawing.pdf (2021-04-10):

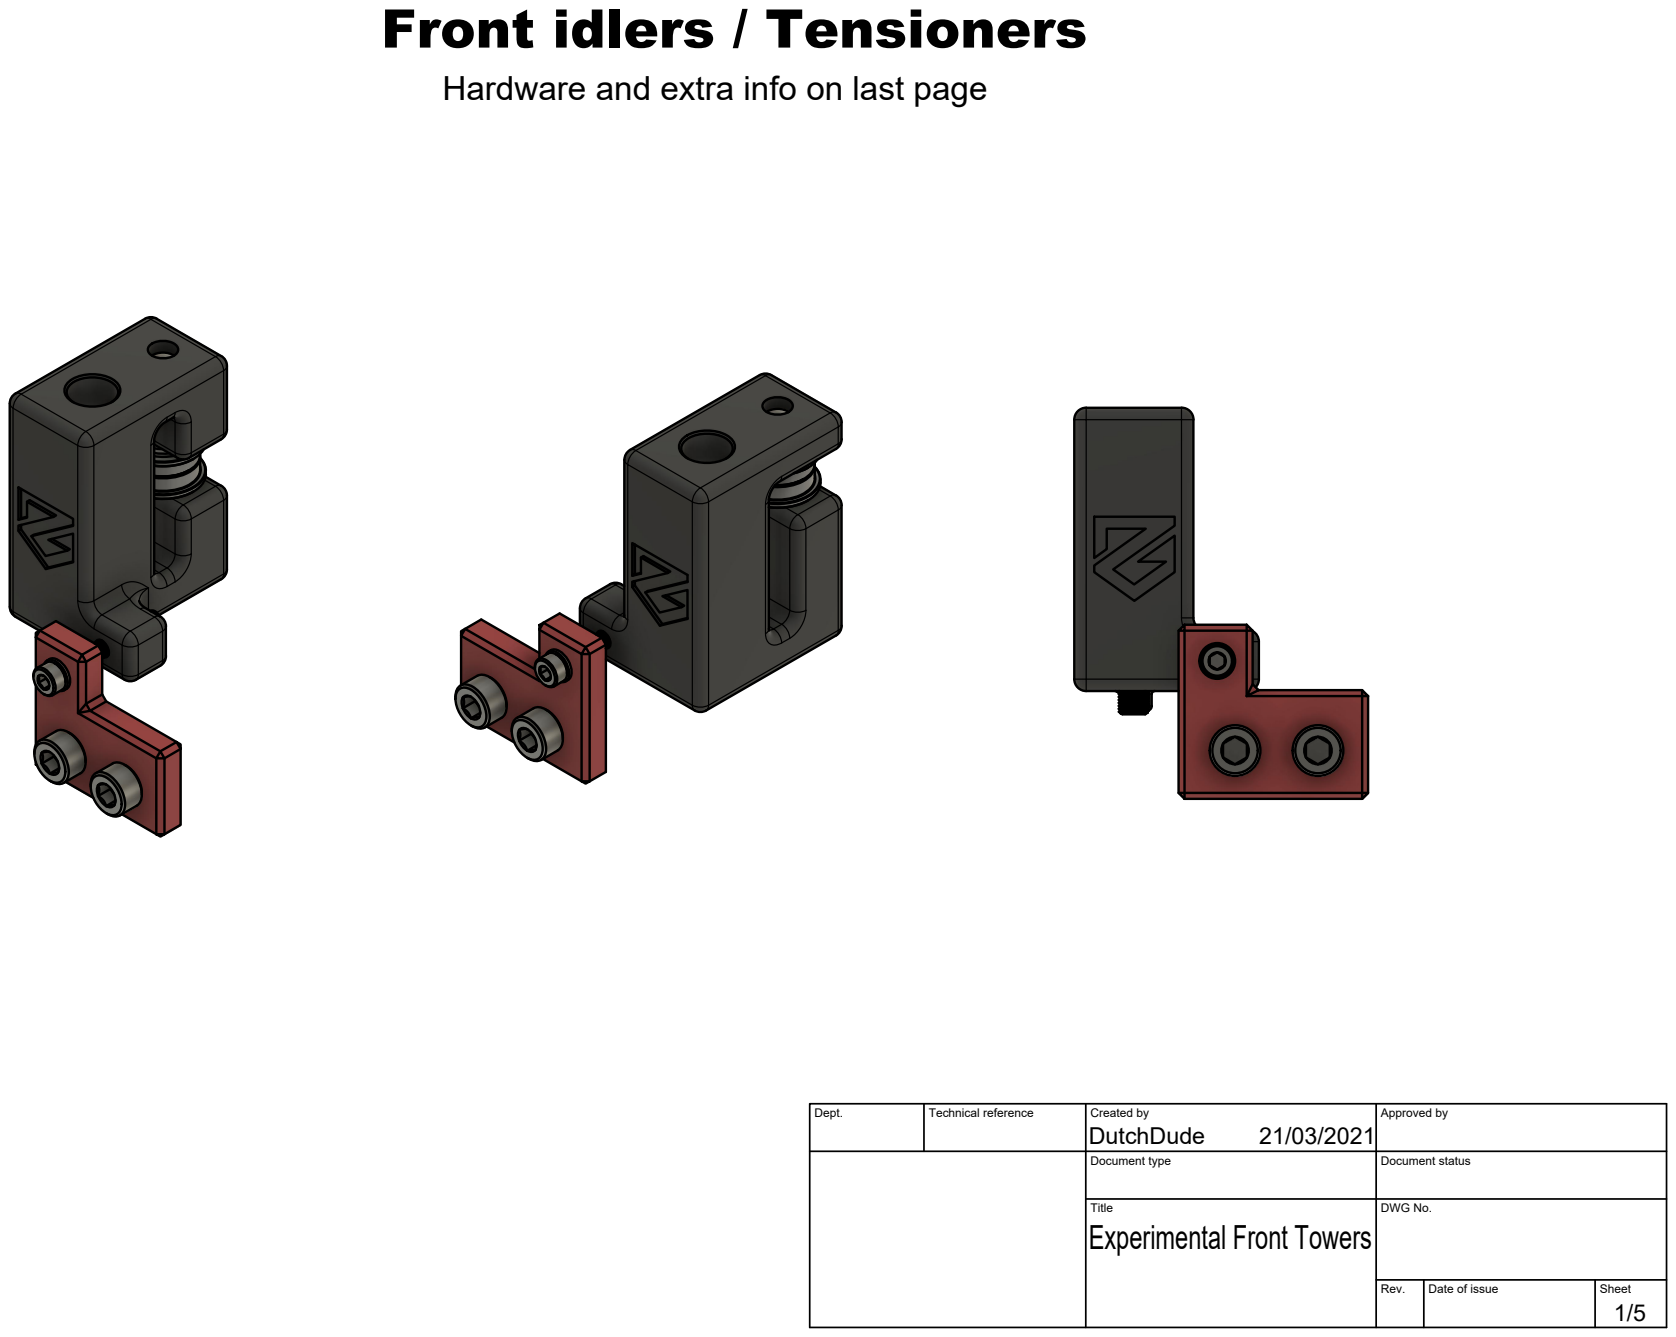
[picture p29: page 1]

Front idlers / Tensioners

Hardware and extra info on last page

Dept. | Technical reference | Created by DutchDude 21/03/2021 | Approved by

Document type | Document status

Title Experimental Front Towers | DWG No.

Rev. | Date of issue | Sheet

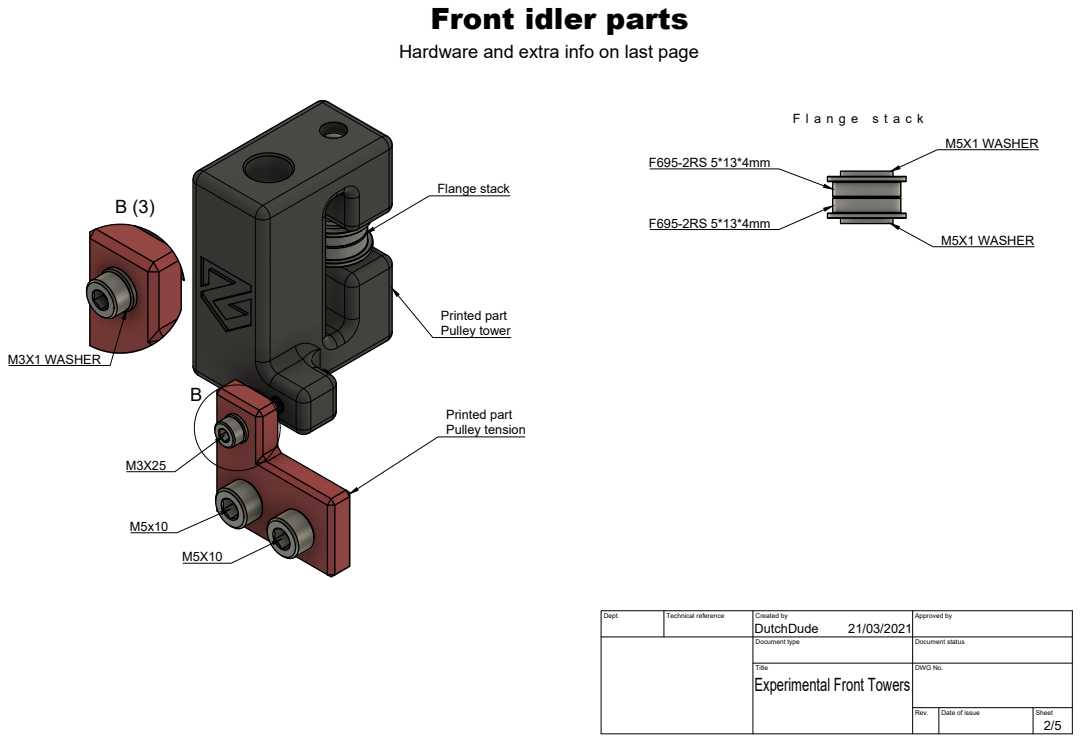
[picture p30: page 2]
M3X1 WASHER; Printed part Pulley tension; Printed part Pulley tower; Flange stack; M5X1 WASHER

Front idler parts

Hardware and extra info on last page

Dept. | Technical reference | Created by DutchDude 21/03/2021 | Approved by

Document type | Document status

Title Experimental Front Towers | DWG No.

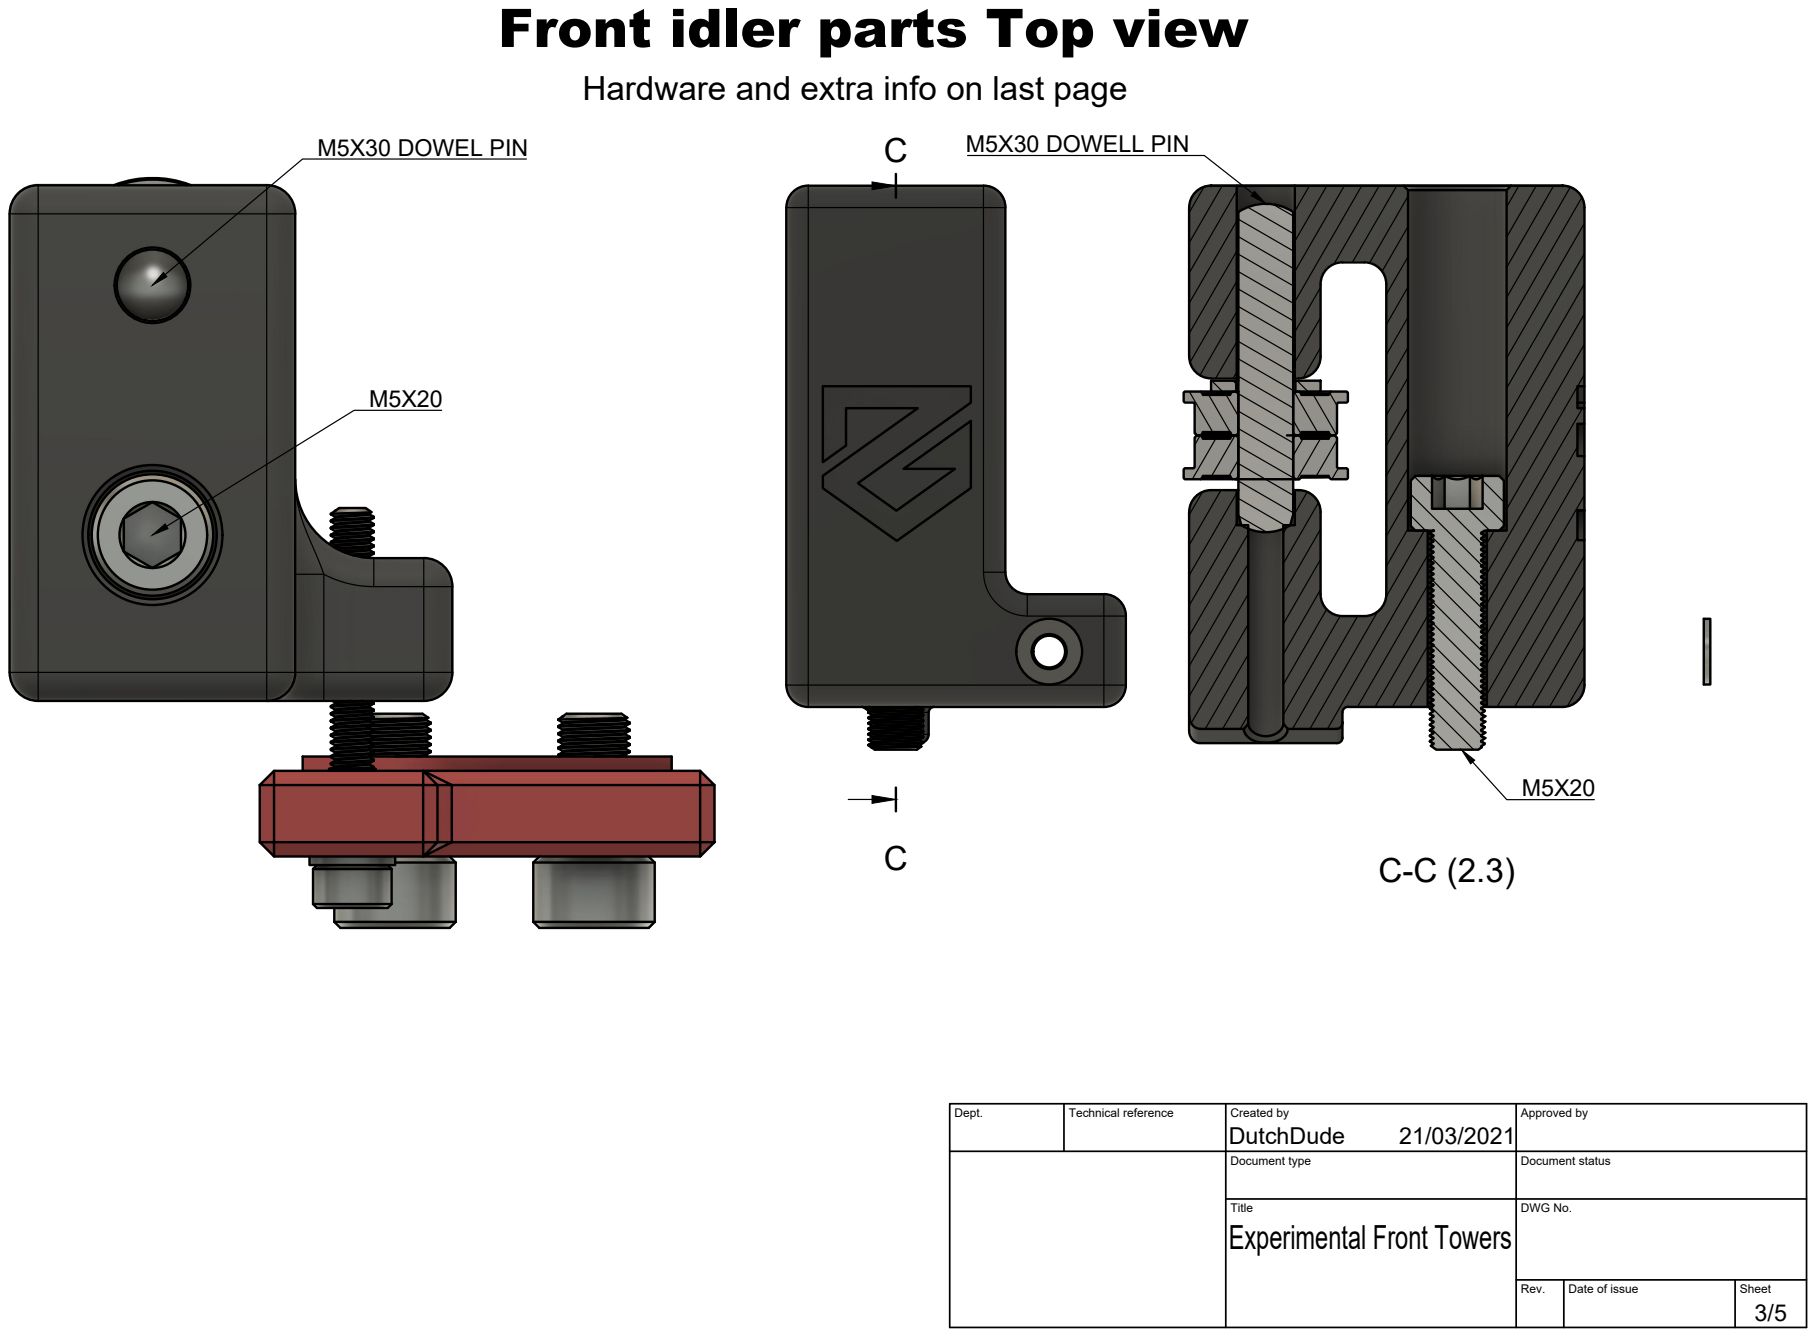
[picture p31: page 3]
M5X30 DOWEL PIN; M5X30 DOWELL PIN

Front idler parts Top view

Hardware and extra info on last page

Dept. | Technical reference | Created by DutchDude 21/03/2021 | Approved by

Document type | Document status

Title Experimental Front Towers | DWG No.

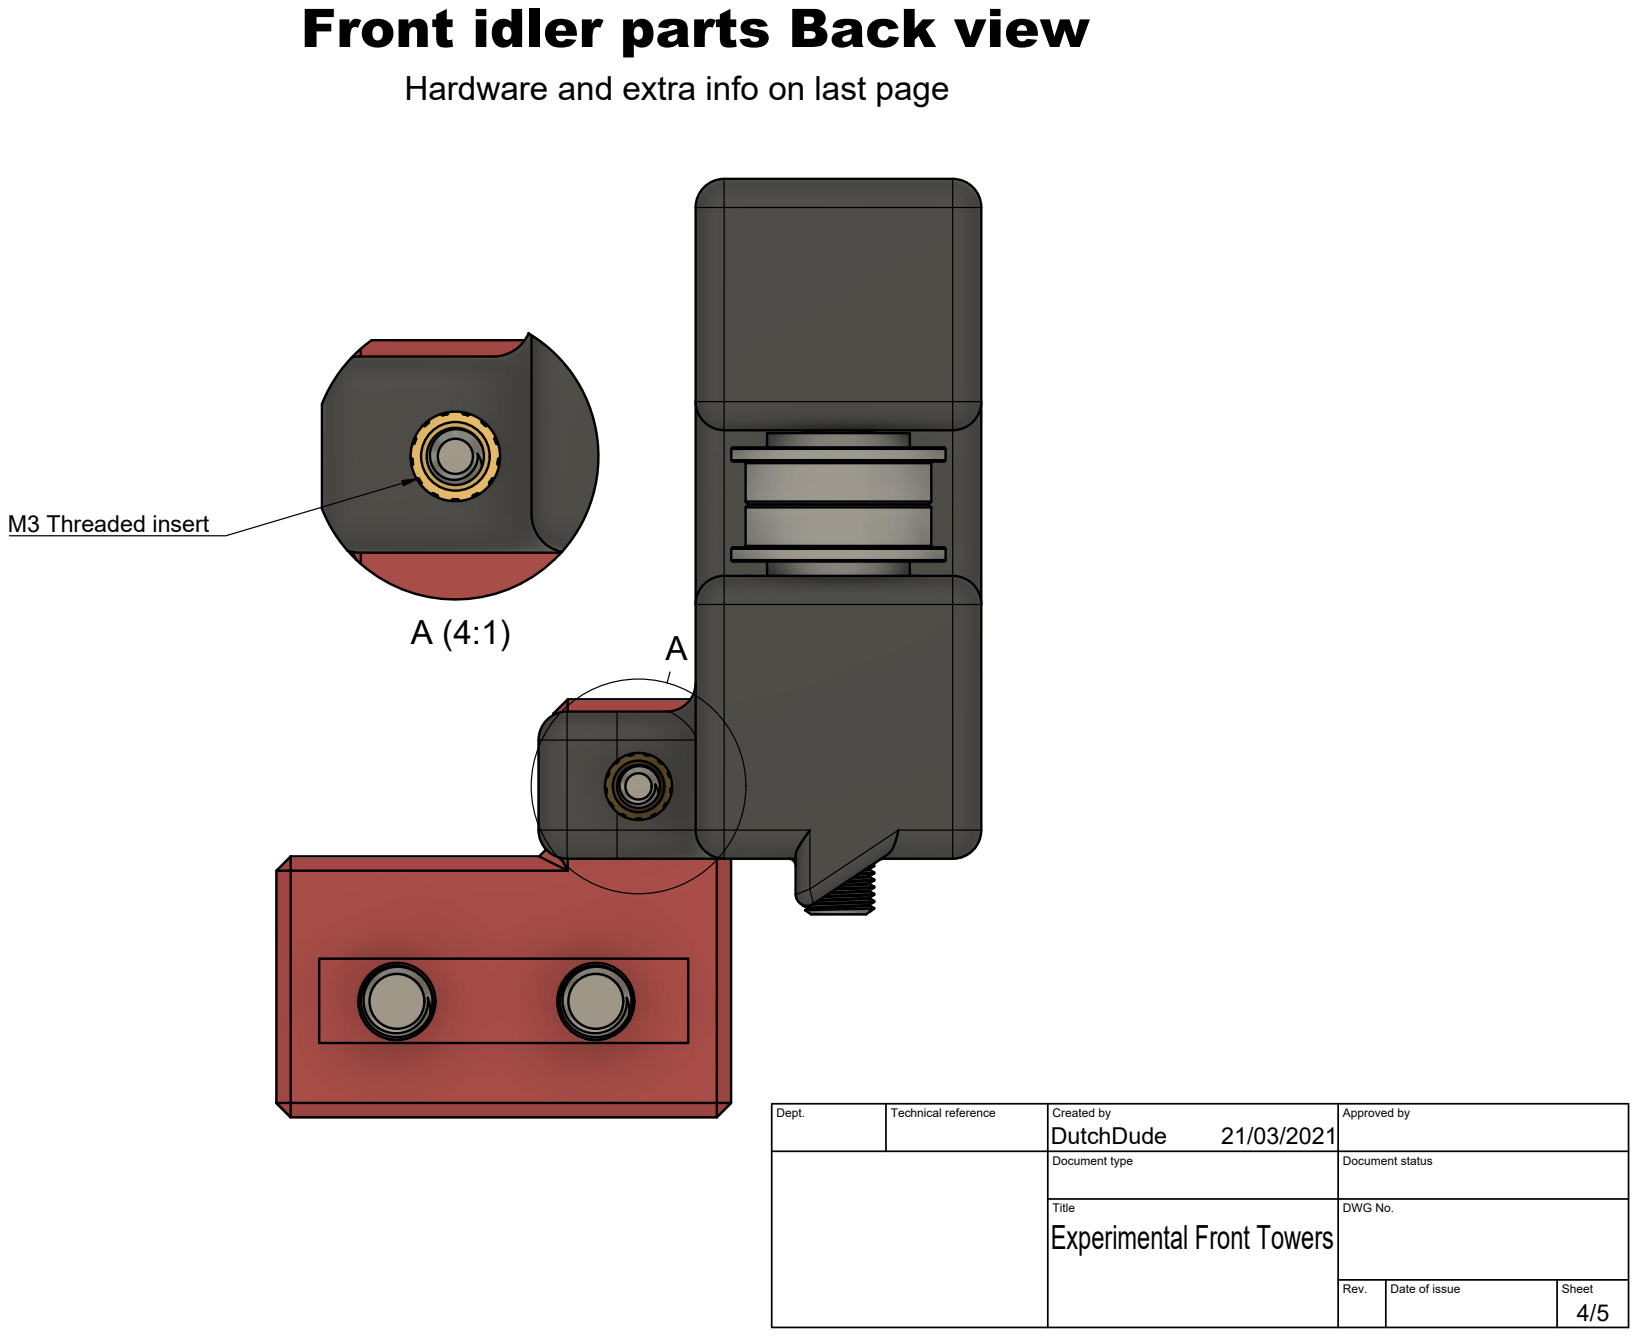
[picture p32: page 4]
M3 Threaded insert

Front idler parts Back view

Hardware and extra info on last page

Dept. | Technical reference | Created by DutchDude 21/03/2021 | Approved by

Document type | Document status

Title Experimental Front Towers | DWG No.

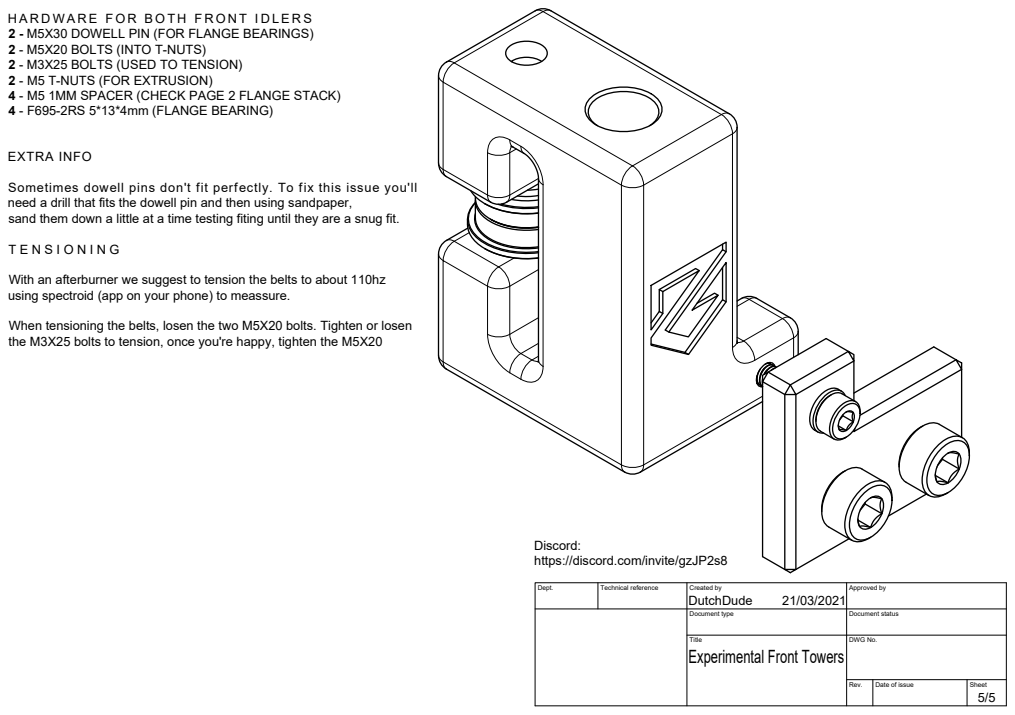
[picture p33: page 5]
EXTRA INFO

2 - M5X30 DOWELL PIN (FOR FLANGE BEARINGS)
2 - M5X20 BOLTS (INTO T-NUTS)
2 - M3X25 BOLTS (USED TO TENSION)
2 - M5 T-NUTS (FOR EXTRUSION)
4 - M5 1MM SPACER (CHECK PAGE 2 FLANGE STACK)
4 - F695-2RS 5*13*4mm (FLANGE BEARING)

Sometimes dowell pins don't fit perfectly. To fix this issue you'll
need a drill that fits the dowell pin and then using sandpaper,
sand them down a little at a time testing fiting until they are a snug fit.

With an afterburner we suggest to tension the belts to about 110hz
using spectroid (app on your phone) to meassure.

When tensioning the belts, losen the two M5X20 bolts. Tighten or losen
the M3X25 bolts to tension, once you're happy, tighten the M5X20

Discord:
https://discord.com/invite/gzJP2s8

Dept. | Technical reference | Created by DutchDude 21/03/2021 | Approved by

Document type | Document status

Title Experimental Front Towers | DWG No.

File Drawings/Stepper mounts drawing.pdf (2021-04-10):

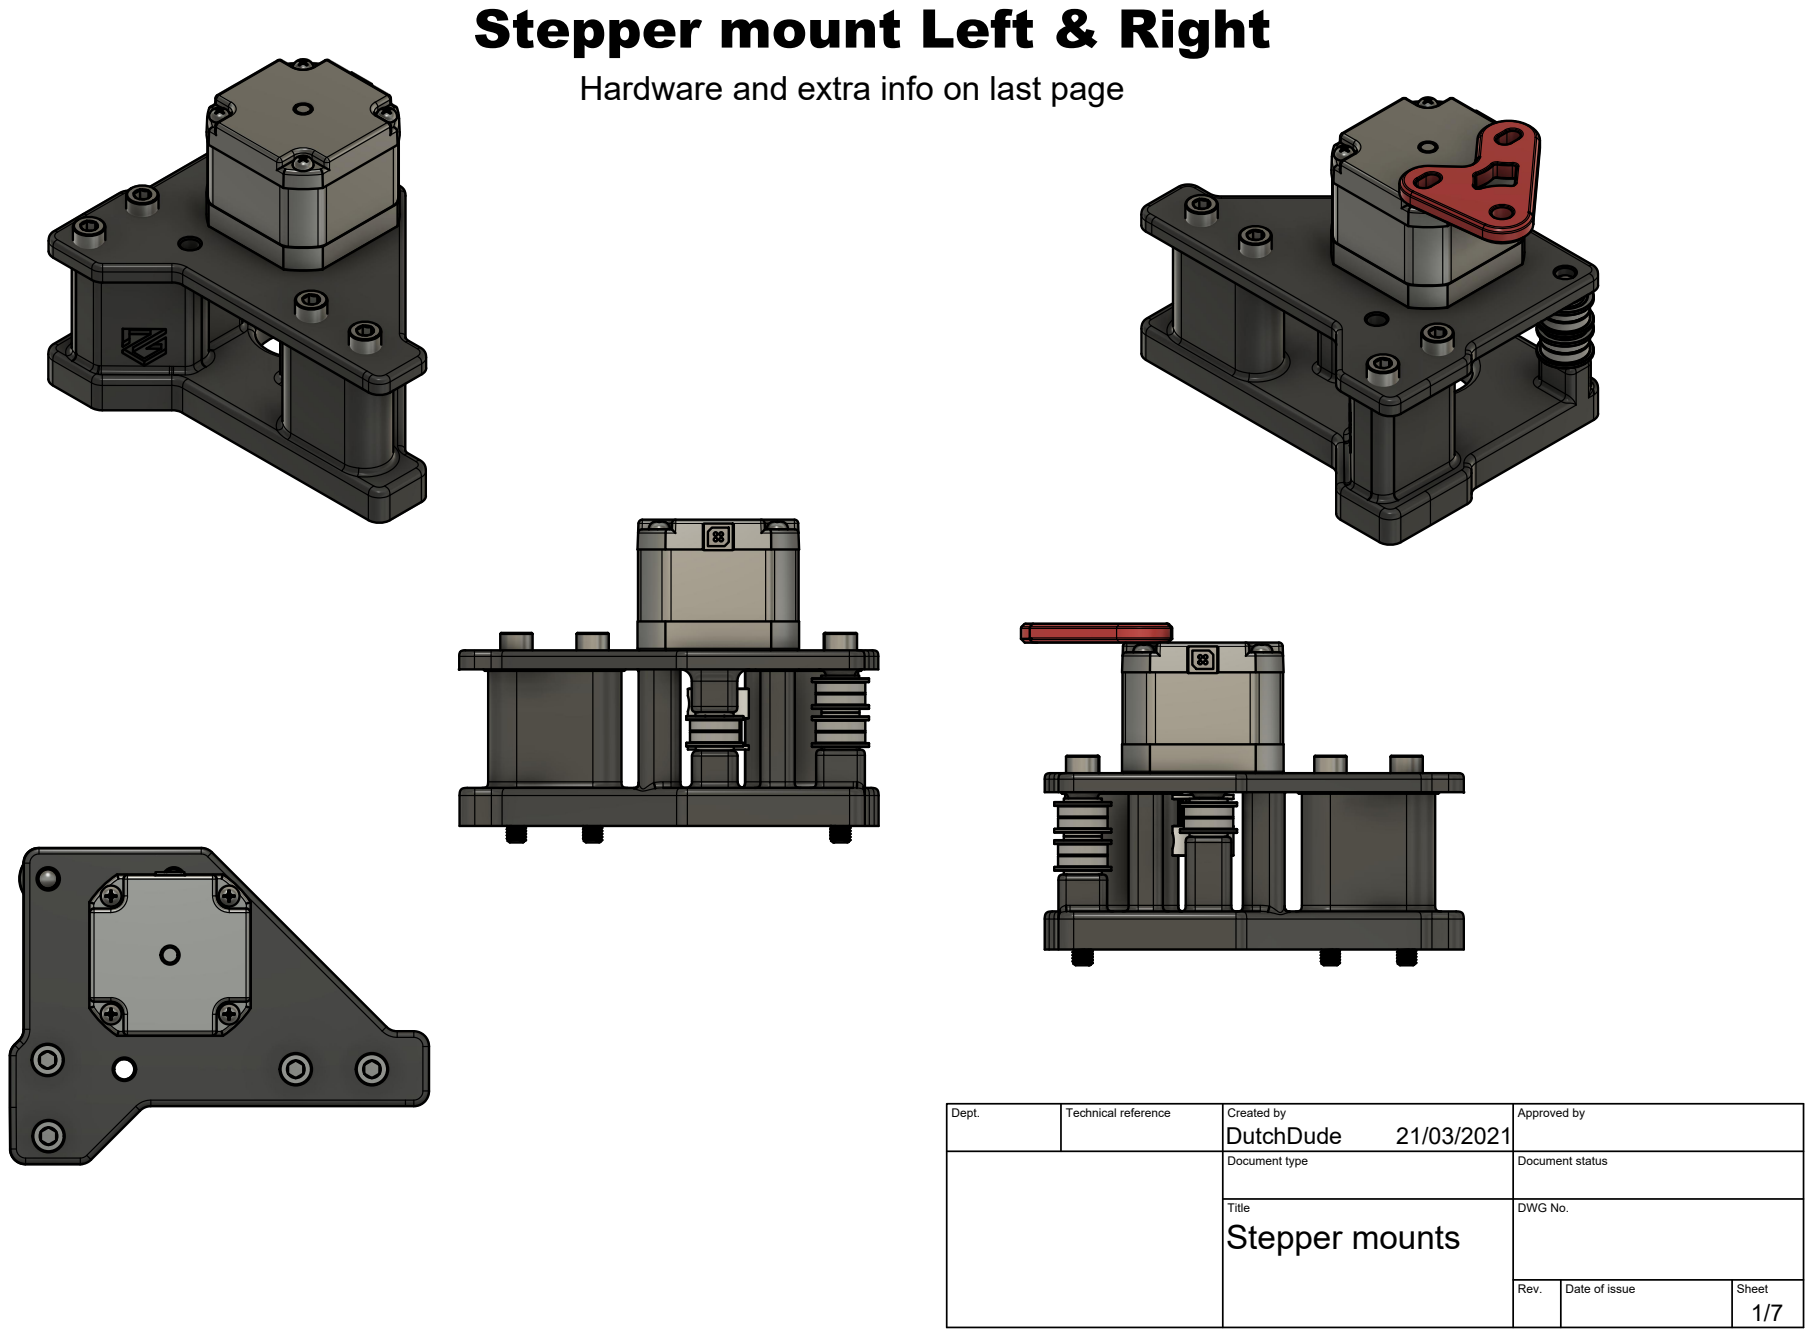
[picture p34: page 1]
Dept.; Technical reference; Created by; Approved by; Document type; Document status; Title; DWG No.; Rev.; Date of issue; Sheet; Stepper mounts

Stepper mount Left & Right

Hardware and extra info on last page

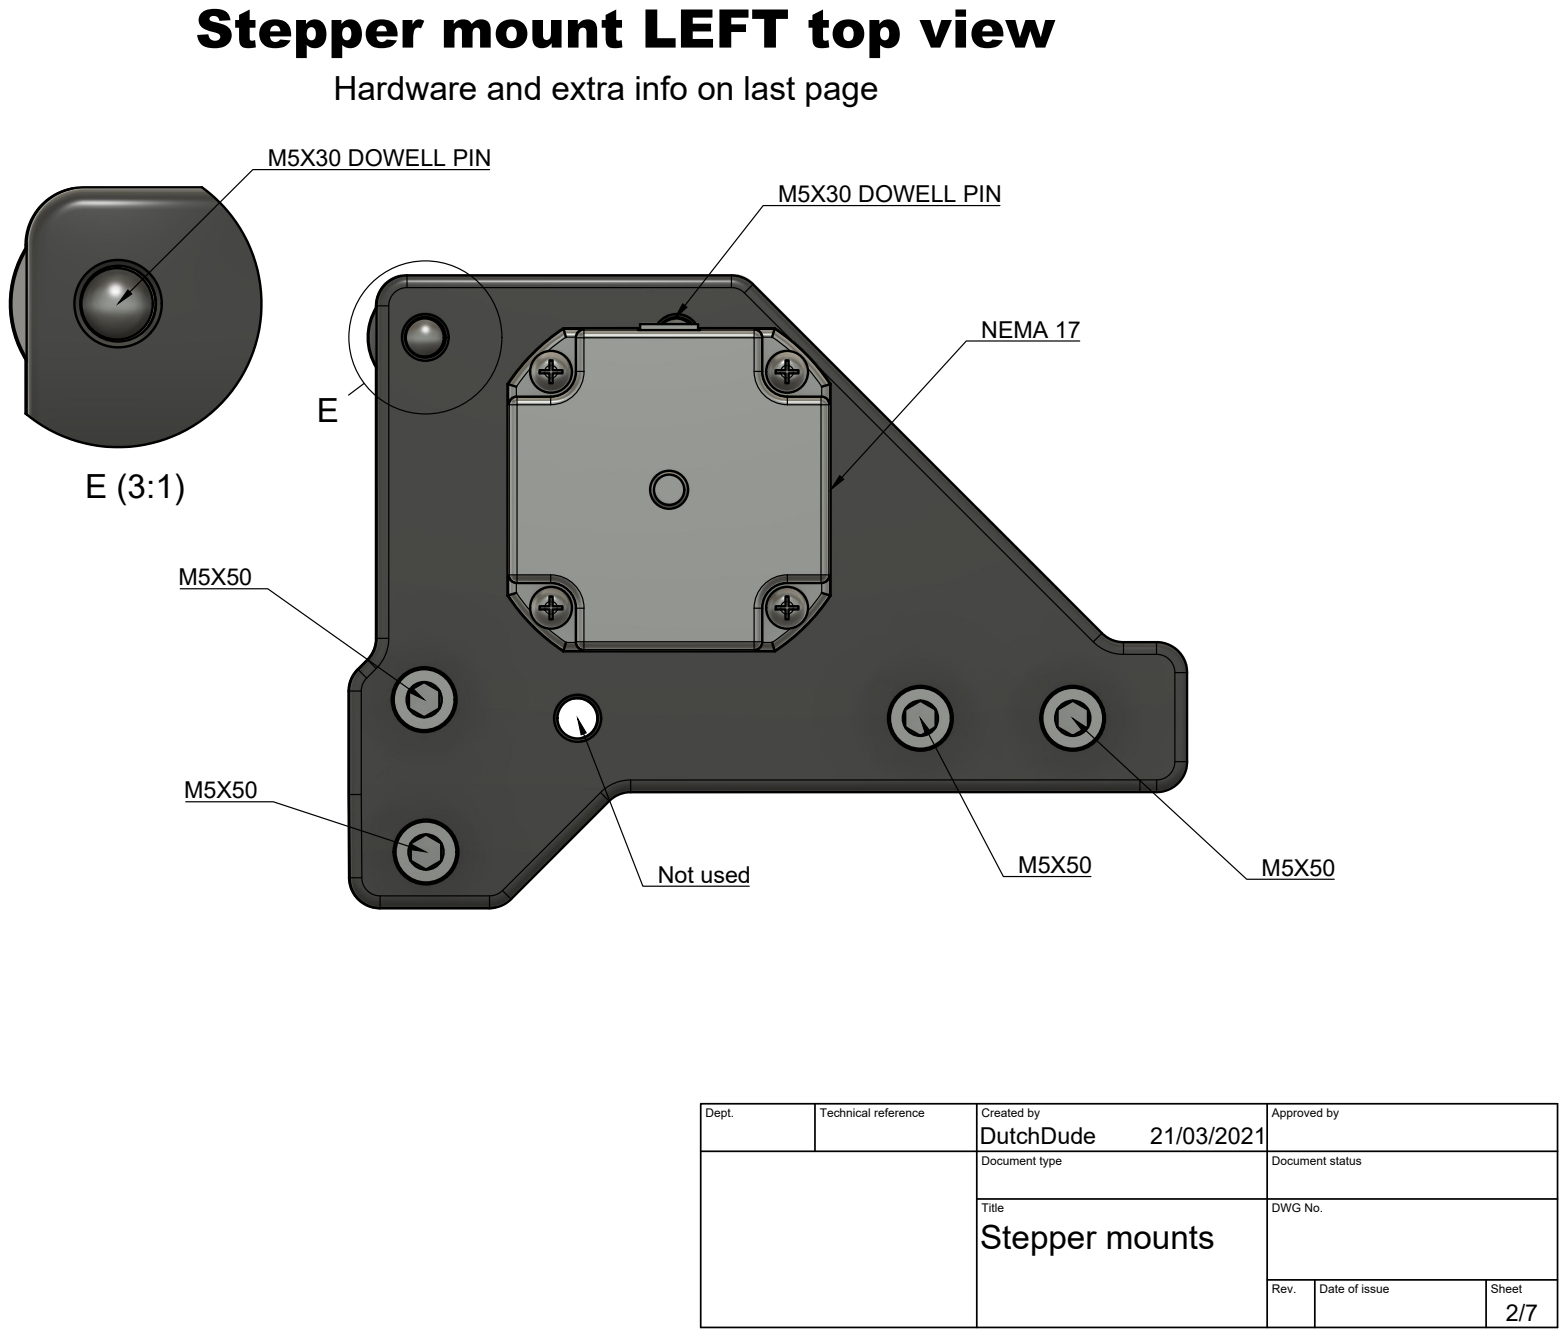
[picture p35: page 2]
M5X30 DOWELL PIN; NEMA 17; Not used

Stepper mount LEFT top view

Hardware and extra info on last page

Dept. | Technical reference | Created by DutchDude 21/03/2021 | Approved by

Document type | Document status

Title Stepper mounts | DWG No.

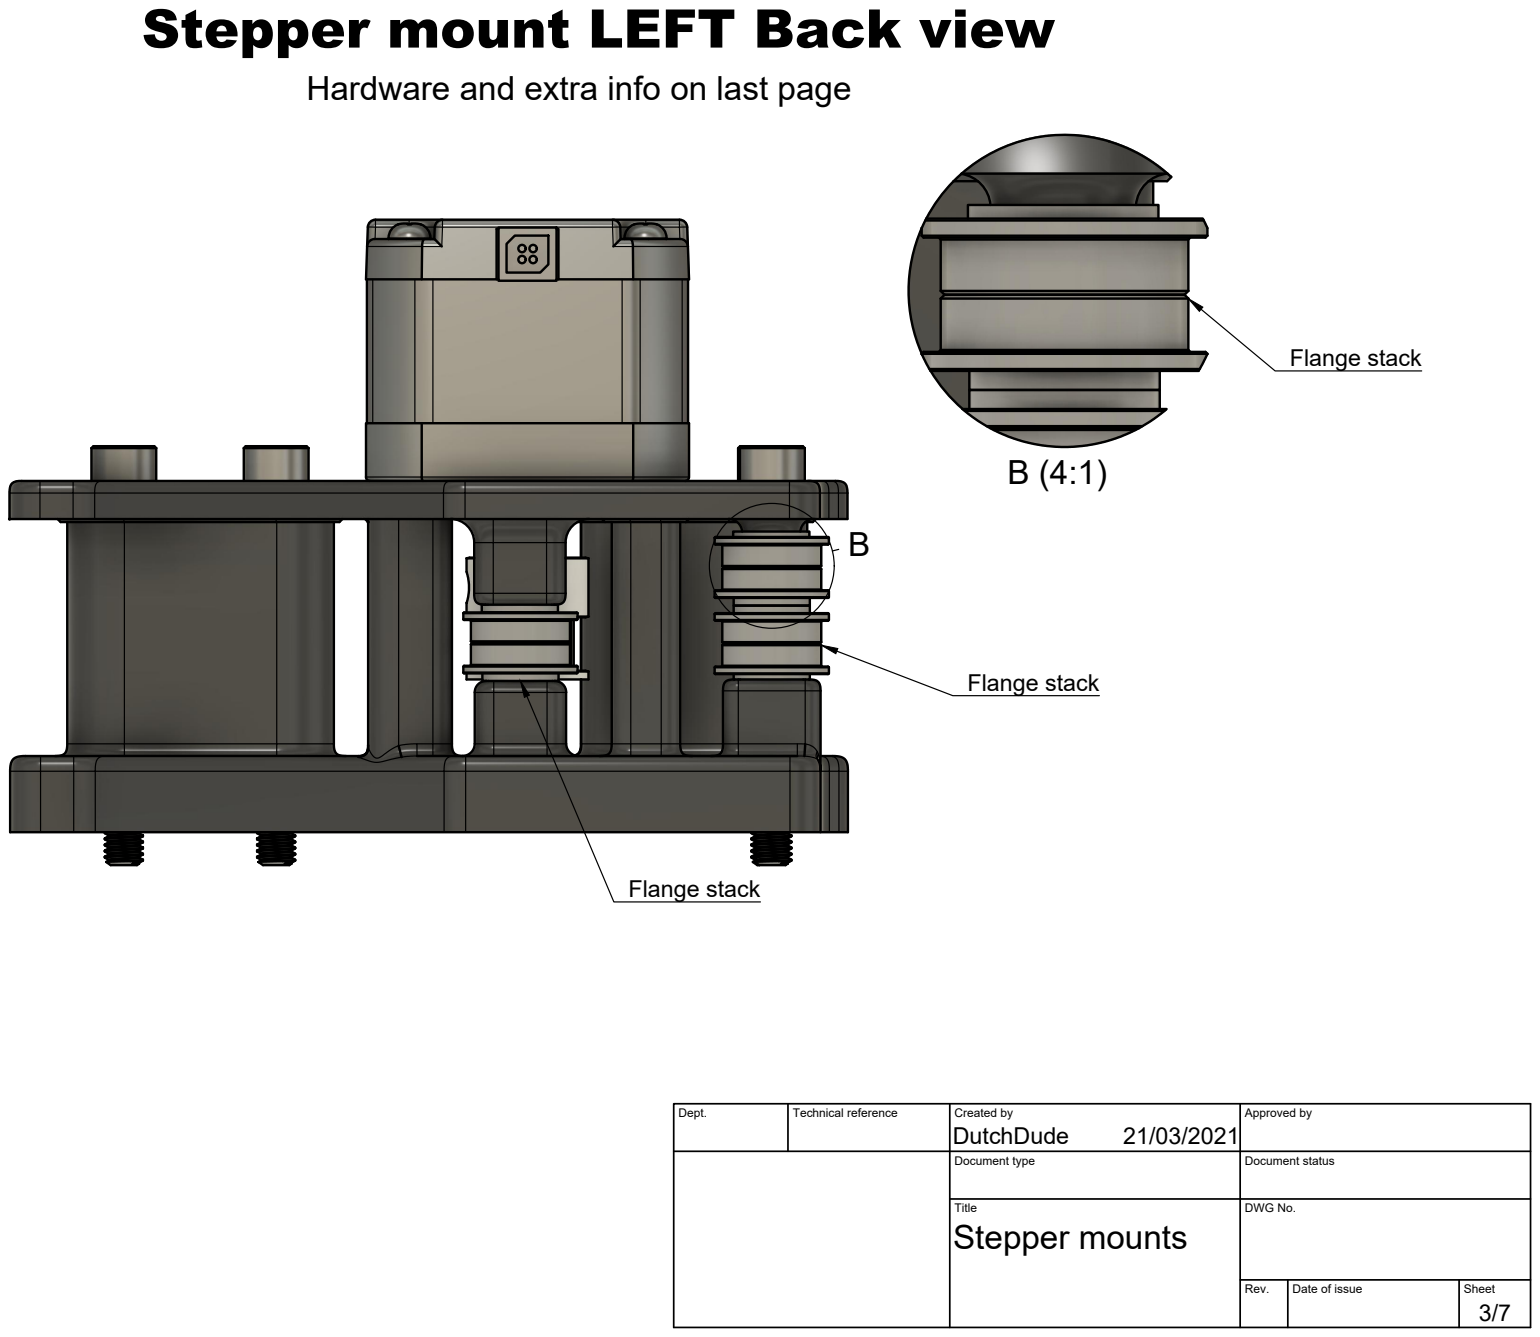
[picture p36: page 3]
Dept.; Technical reference; Created by; Approved by; Document type; Document status; Title; DWG No.; Stepper mounts; Flange stack

Stepper mount LEFT Back view

Hardware and extra info on last page

GT2 20T Pulley 6mm

Stepper mount LEFT SIDE view

Hardware and extra info on last page

Dept. | Technical reference | Created by DutchDude 21/03/2021 | Approved by

Document type | Document status

Title Stepper mounts | DWG No.


Stepper mount LEFT bottom view

Hardware and extra info on last page

Dept. | Technical reference | Created by DutchDude 21/03/2021 | Approved by

Document type | Document status

Title Stepper mounts | DWG No.


Stepper mount Right

Hardware and extra info on last page

The right stepper mount uses the exact same hardware as the left
stepper mount.

Optional cable chain mount

Installation of the cable chain mount onto the NEMA17 stepper is
fully optional.

Dept. | Technical reference | Created by DutchDude 21/03/2021 | Approved by

Document type | Document status

Title Stepper mounts | DWG No.

M5 - 1 MM WASHER; M5 - 1MM WASHER

8 - M5X50 BOLTS (INTO T-NUTS)
8 - M5 T-NUTS (FOR EXTRUSION)
6 - M3X20 (ATTACHES STEPPER)
4 - M5X30 Dowel Pins (FOR FLANGE BEARINGS)
12 - M5 1MM SPACER (BETWEEN FLANGE BEARINGS)
12 - F695-2RS 5*13*4mm (FLANGE BEARING)

Sometimes dowell pins don't fit perfectly. To fix this issue you'll
need a drill that fits the dowell pin and then using sandpaper,
sand them down a little at a time testing fiting until they are a snug
fit.

Discord:
https://discord.com/invite/gzJP2s8

Dept. | Technical reference | Created by DutchDude 21/03/2021 | Approved by

Document type | Document status

Title Stepper mounts | DWG No.

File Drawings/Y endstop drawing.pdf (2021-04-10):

Y Endstop

Hardware and extra info on last page

Dept. | Technical reference | Created by DutchDude 21/03/2021 | Approved by

Document type | Document status

Title ENDSTOP Y | DWG No.

Rev. | Date of issue | Sheet

PRINTED PART; Front view

Hardware and extra info on last page

Dept. | Technical reference | Created by DutchDude 21/03/2021 | Approved by

Document type | Document status

Title ENDSTOP Y | DWG No.

KW 10 MICROSWITCH; Back view; M5 T-NUT

Hardware and extra info on last page

ENDSTOP CABLE PATH

Dept. | Technical reference | Created by DutchDude 21/03/2021 | Approved by

Document type | Document status

Title ENDSTOP Y | DWG No.

EXTRA INFO

HARDWARE FOR Y ENDSTOP

2 - M5X12 BOLTS (INTO T-NUTS)
2 - T-NUTS (FOR EXTRUSION)
1 - KW10 MICROSWITCH (ENDSTOP)

You could skip this part if you're using sensorless homing

Discord:
https://discord.com/invite/gzJP2s8

Dept. | Technical reference | Created by DutchDude 21/03/2021 | Approved by

Document type | Document status

Title ENDSTOP Y | DWG No.

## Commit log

2021-02-03 Modified Voron Afterburner mount
    This mount will fit MGN12H rails and is a highly modified version Voron Afterburner mount original can be found here: https://github.com/VoronDesign/Voron-Afterburner.
    Don't forget to also print the belt clamp x 2, these are also modified.
    [belt_clamp_x2.stl, x_carriage_frame_left.stl, x_carriage_frame_right.stl]
2021-03-21 Rename main folder
    Just a rename
    [belt_clamp_x2.stl, x_carriage_frame_left.stl, x_carriage_frame_right.stl]
2021-03-21 Create Y endstop drawing.pdf
2021-03-21 Initial drawing
    New drawing, front tensioners
2021-04-10 Initial OPEN BETA Stl files
    STL Files for OPEN beta
    [CLIPX2.stl, Left half.stl, Pulley_tension_left.stl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]
2021-04-10 Rail Alignment tool - Print twice
    This tool will help you align a MGN12H rail with a 20x20 extrusions.
    Credits: https://www.blvprojects.com/
    [Rail alignment tool x 2.stl]
2021-04-10 Added missing hardware info
    Hardware list missing the size of the T-NUT, fixed.
2021-04-12 Small fixed
    Drawing files:
    X Assembly has been updated, typo on the last page + made more readable.
    Afterburner mount drawing updated to small changes in model.
    STLs:
    Gantry bottom files (left & right) a Slightly bigger hole for M5 Hex nuts + bevel for first layer.
    Afterburner MGN12H mount, moved alignment tool to the inside, feedback tells that printing overhangs with ABS is not easy for everyone
    [Left half.stl, Right half.stl]
2021-04-24 Missing stls
    Added Y endstop stl, missing from files.
    Made a 30x30 calibration cube:
    Bottom hole is for a 5x30mm dowel pin.
    Top mid hole is for a heat insert.
    Next to the center hole there is a slot for the M5 Nut.
    [Y_Endstop.stl, ZeroGCube30x30.stl]
2021-05-24 Step file release
    Step file release, BOM will be made later.
    [right_stepper_chain_mount_generic_optional.stl]
2021-06-22 Callibration cube renders
    The calibration cube contains a heat insert on top, m5 nut and a dowel pin in the bottom.
2023-01-11 Removing STLs since these are outdated.
    Find the new once on our website https://docs.zerog.one/manual/build/mercury_eva
    [BOTTOM_LEFT.stl, Bottom_right.stl, CLIPX2.stl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]
